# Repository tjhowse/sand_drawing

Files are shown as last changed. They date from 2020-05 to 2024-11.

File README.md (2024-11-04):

# Huh?

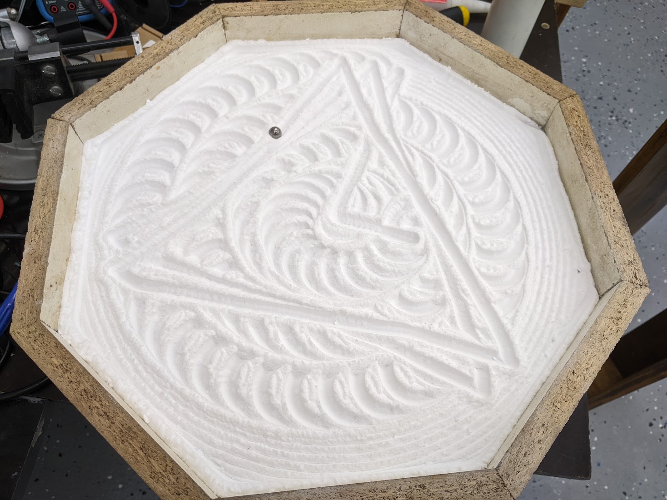
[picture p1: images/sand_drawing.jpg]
a photo of the sand drawing robot


So you've been reading about all the benefits of this "mindfulness" thing and you want to give it a try.
You do some research and learn it requires "meditation", "introspection" and other kinds of tedious woo.
Who has time for that? It's {current_year} for christ's sake! I don't want a tiny tray of rocks and sand
on my desk to rake around. Surely there's some turn-key solution to this problem already.

That's what this project is for. Outsource responsibility for an ordered mind to make more time for the important things, like computer games. And croissants.

# Oh

This project (will contain/contains) all the knowledge you will need to build your own sand drawing robot. Heavily inspired by the likes of [Sandsara](https://www.kickstarter.com/projects/edcano/sandsara) and [Sisyphus](https://sisyphus-industries.com/). It's a robot that moves a ball around in a bed of sand to draw cool patterns. The patterns can be updated via wifi, and it can cycle through them, you can create your own, etc, etc. This project is open source, cheap, and hopefully as easy as possible to build.

# Building it

## Skills required

This isn't a Lego set. You'll need to have access to the following skills:

* Basic woodworking,
* Intermediate soldering,
* Following technical instructions,
* Drilling a hole sideways through steel rod,
* Recovering from setbacks.

I'll do my best to make the instructions as comprehensive and comphrehensible as I can. I appreciate any and all feedback.

## Videos

[Playlist on Youtube.](https://www.youtube.com/playlist?list=PLT7ckgz8vcoY2YFqqQTA0kUofwehtqQul) Maybe worth watching.

## PCB

The PCB is quite simple and cheap. PCBWay generously sponsored a production run of the v1.2 PCBs and they came out perfect. You can order the PCB using [this link](https://www.pcbway.com/project/shareproject/Sand_Drawing_Robot_control_board_344d0ab2.html) and I'll get a small cut. PCBWay asked me to review the board in a youtube video and link it in the readme, but required no further quid pro quo.

## Build logs

For now the build logs are on [my wiki](https://wiki.tjhowse.com/doku.php?id=projects:sand_drawing:overview). Over time they'll morph into actual instructions and end up in this repo.

## Bill of materials

None of these parts are particularly hard to find. Check ebay and whatnot. Try to buy local if you can. It's hard to guess how much it will all cost in total, but I've tried to design everything to be as economical as possible. Excluding the housing I would (very roughly) estimate the BoM to come out to around AUD$200. The housing could be as cheap as AUD$50 (Melamine board, polycarbonate) or as expensive as you want, with lacquered hardwood and tempered glass.

    These bills of material are slightly out of date. Consult the youtube videos.

### Mechanical
| Item | Type | Count | Note |
| ---- | ---- | ----- | ---- |
| Laser cut parts | Various | Many | The current best solution is made from 3mm laser cut plywood. A 3D printed variant is quite possible. |
| Stepper pulley | GT2-20, 12.35mm high | 2 | My steppers had pulleys from the factory. |
| Belt | S2M belt 120mm | 2 | S2M ≈ GT2. |
| Belt | S2M belt 278mm | 1 | |
| Shaft 1 | 8mm x 90mm | 1 | Mild steel is easier to cross-drill than stainless. |
| Shaft 2 | 8mm x 33mm | 1 | |
| Bearing | 608 | 6 | Cheap skate bearings are fine. |
| Washers | 8mm ID, 15.7mm OD | 5 | OD not critical, but it must not rub on outer race of bearings. |
| Washers | 3mm ID, 6.8mm OD | 12 | |
| Bolts | M3x12mm | 8 | I used all 20mm and cut them to length. |
| Bolts | M3x20mm | 2 | |
| Nylock nuts | M3 | 2 | Nylock not critical. |
| Pins | 2mm diameter | 5 | Roll pins would be best, I used nails. +1 extra for pinning shaft 1 into the bearings. |
| Magnets | 12mm diameter, 2mm high neodymium | 2-4 | Situational dimensions. Get a variety of sizes to aid experimentation. |
| Cable ties | 200mm x 4.6mm Nylon | 2 | Dimensions not critical. |

### Electrical
| Item | Type | Count | Note |
| ---- | ---- | ----- | ---- |
| Microcontroller | ESP-WROOM-32D | 1 | Wifi and bluetooth built-in |
| Stepper motor | NEMA-17 | 2 | 200 steps/revolution, around 40mm long, at least 30 N.cm of holding torque. It's not critical, really. |
| Stepper driver | Pololu pinout | 2 | A4988, DRV8825 or TMC2100 in [increasing order of preference](https://github.com/tjhowse/sand_drawing/issues/6) |
| PCB | Custom made | 1 | The design is [here](./pcb/sand_drawing). It's easier and cheaper to have one made than you [might imagine](./pcb/sand_drawing/README_PCB.md).
| Hall effect sensors | SS49E | 2 | Used for detecting arm position. |
| PSU | 12v DC 1A | 1 | A wall wart should be fine. |
| Stepper driver socket | 16x1 2.54mm female | 2 | https://au.rs-online.com/web/p/pcb-sockets/2304893/ |
| Stepper motor socket | 4x1 3.5mm | 2 | https://au.rs-online.com/web/p/pcb-headers/8971039/ |
| Stepper motor plug | 4x1 3.5mm | 2 | https://au.rs-online.com/web/p/pcb-terminal-blocks/8971004/ |
| Optoswitch socket | 3x1 3.5mm | 2 | https://au.rs-online.com/web/p/pcb-headers/8971020/ |
| Optoswitch plug | 3x1 3.5mm | 2 | https://au.rs-online.com/web/p/pcb-terminal-blocks/8971001/ |
| Power socket | 2x1 3.5mm | 1 | https://au.rs-online.com/web/p/pcb-headers/8971026/ |
| Power plug | 2x1 3.5mm | 1 | https://au.rs-online.com/web/p/pcb-terminal-blocks/8970998/ |
| Buttons | 6mm | 2 | https://au.rs-online.com/web/p/tactile-switches/1359534/ |
| UART Header | 3x1 2.54mm male | 1 | https://au.rs-online.com/web/p/pcb-headers/8967364/ |
| 12VDC Barrel socket | 2.1mm pin | 1 | https://au.rs-online.com/web/p/dc-power-sockets/0448370/ |

### Enclosure
| Item | Type | Count | Note |
| ---- | ---- | ----- | ---- |
| Base | Wooood? | 1 | Holds the steppers and circuitry. |
| Top | Wooood? | 1 | Any convex polygon should work. |
| Bed | Glass? | 1 | |
| Lid | Glass | 1 | |
| Sand | Sand | 31378908 | < 100 μm grains, dry.

# Flashing

To flash the software onto the ESP32 you'll need to use the provided scripts `flash32.sh` and `write32.sh`. You'll have to update them with the current version of micropython and the device name of your serial port adapter. When flashing micropython you'll need to hold down the IO0 button while connecting power, then release it five or so seconds after powering on. You can then run `flash32.sh` and it'll write the "OS" onto the chip. Then you can repower again and run `write32.sh` to load the project's scripts onto the board.

# Communication
The ESP-WROOM-32 has wifi and BLE built in. Currently the robot connects to a wifi network, then an MQTT server, to receive commands. Bluetooth should also be possible in the future.

## MQTT Topics
There are a few topics that the robot listens to. Each topic starts with `{secrets.mqtt_root}/sand_drawing/`. I suggest you publish patterns/generators with the retain bit so the robot starts up and then begins that pattern.
| Topic | Example payload | Description |
| ----  | --- | --- |
| `pattern` | `G28 X,G28 Y,G1 X0 Y175,G1 X123 Y123,G1 X175 Y0,J0 2` | Starts drawing the pattern defined by the GCODE in the payload. |
| `generator` | [Here](./pub_gen.py#L82) | Starts drawing the pattern defined by the generator in the payload. See below for details on generators. |
| `save_generator` | `1.pat {generator string}` | Saves the generator to a file in the robot's flash storage. The file extension must be `.pat`. A blank string will erase the generator. |
| `run_generator` | `1.pat` | Starts drawing the previously saved generators. |
| `delete_generator` | `1.pat` | Deletes a generator saved to the robot. |
| `list_generators` | N/A | Publishes a list of filenames to `generator_list` topic. |
| `shuffle_generators` | `3600` | Randomly picks a saved generator and starts drawing it. Optionally provide a number of seconds before choosing another random generator |

# Configuration
There are some files you'll need to edit before your robot will work for you, probably.
[#TODO populate this section.](https://github.com/tjhowse/sand_drawing/issues/13)

# Pattern definition
There are currently two ways to design patterns for the robot.

## GCODEs
This is a sequence of coordinates that define the path of the ball, as well as changing modes and looping. The following GCODES are currently supported. GCODES are separated by a comma.

| Name | GCODE | Example | Description |
| ---- | ----- | --- | --- |
| Home axis| G28 | `G28 X,G28 Y,` | Home either the X or Y axis. Any command that needs an absolute position reference will fail unless both axes have been homed first. |
| Move | G1 | `G1 X10 Y50 S100,` | Go to the X and Y coordinates specified at 100mm/s. Currently the [speed field is ignored](https://github.com/tjhowse/sand_drawing/issues/4). The G1 movement mode carefully tracks every step and should be perfectly accurate if your steppers do not slip. |
| Fast move | G0 |  `G0 X10 Y50 S100,` | Same as G1 however the step signal square wave is generated using PWM so some resolution is lost. At time of writing it is not well-supported. It's really fast though. |
| Coordinate mode | G16 | `G16 0,` | This setting is used to control the interpretation of the `X` and `Y` parameters in the G0 and G1 commands. `0`: Raw speed, `1`: Raw angle, `2`: Cartesian (Default), `3`: Polar (unimplemented) |
| Jump | J0 | `J0 3,` | This jumps to the specified line in the GCODE-defined pattern. Used for creating loops. |
| Absolute coordinate mode | G90 | `G90` | Puts the robot into absolute movement mode. Coordinates in G0/G1 commands are interpreted as absolute position references. (Default) |
| Relative coordinate mode | G91 | `G91` | Puts the robot into relative movement mode. Coordinates in G0/G1 commands are interpreted as movement vectors from the previous position. |

## Generators
You can define a pattern using a python generator function. [Examples here](./pub_gen.py). This is probably the best option for non-trivial patterns.

### Tread lightly
Keep the target hardware in mind when writing generators. It's very resource-constrained. Try to limit RAM usage, and think hard before `import`ing anything. There are some [helper functions](./generator_libs.py) and [constants](./constants.py) in-scope that you can use.

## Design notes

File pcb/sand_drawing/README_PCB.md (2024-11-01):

# PCB Changelog

## v1.2
### Changes
* Fixing footprints for new vreg circuits
* Updated electronics BoM

## v1.1
### Changes
* Connected all stepper driver control pins to ESP
* Changed vreg circuit from an AMS1117-3.3 to an AP63203 with higher current capacity
* Add thermal relief to ESP32 ground pins for easier hand soldering

## v1.0
### Changes
Initial implementation

### Bugs
* Shouldn't use GPIO9 - it is used internally too.
* Pin 7 (IO35) is input-only, can't use that for A2D. - Done.
* Must pull SLP and RST on stepper drivers high. - Done.
* vreg too small, or wired wrong? Only outputs 2.7 Vout at 12 Vin - Done.
* Make sure opto inputs are on ADC-friendly pins. - Done
* Reduce width of ground tie on ESP for easier soldering. - Done.

# ESP-WROOM-32 notes

Minimal implementation on page 15:
https://www.espressif.com/sites/default/files/documentation/esp32-wroom-32d_esp32-wroom-32u_datasheet_en.pdf
A minimal wiring demo:
https://www.youtube.com/watch?v=J10J_7Ap6Oo

# EMC2100 SilentStepStick

These things seem like a bit of a pain in the arse, TBH. I hope they're good.

FAQ:
https://learn.watterott.com/silentstepstick/faq/

# Manufacture

This board is designed for manufacture with PCBWay or JLC. Parts selection, BOM and whatnot are set up for easy manufacture. You should only need to solder on the ESP-WROOM-32D (if using JLC) and headers. All the fiddly little SMD stuff can be done for you, quite cheaply.

## PCBWay-specific notes

You should be able to order a PCB with all the SMD components, including the ESP32) with (this)[https://www.pcbway.com/project/shareproject/Sand_Drawing_Robot_control_board_344d0ab2.html] link. I get a 10% cut.

## JLC-specific notes

If you regenerate the footprint position files you'll need to manually change the header line from:
```
Ref,Val,Package,PosX,PosY,Rot,Side
```
To:
```
Designator,Val,Package,Mid X,Mid Y,Rotation,Layer
```
as per https://support.jlcpcb.com/article/84-how-to-generate-the-bom-and-centroid-file-from-kicad

Odds are you'll need to change the rotation of U2 to 180 degrees, too. Be SUPER CAREFUL at EACH STEP
of the ordering process and you should be OK.

See also https://support.jlcpcb.com/article/84-how-to-generate-the-bom-and-centroid-file-from-kicad for
instructions on how to properly format the BOM spreadsheet for JLC PCB to ingest.

As of 2020-05-30 the price to have five of these boards made, with VREG, resistors, capacitors and diodes
populated was AUD$22.60. This included some discounts and whatnot. Express postage to Australia was AUD$28.03.

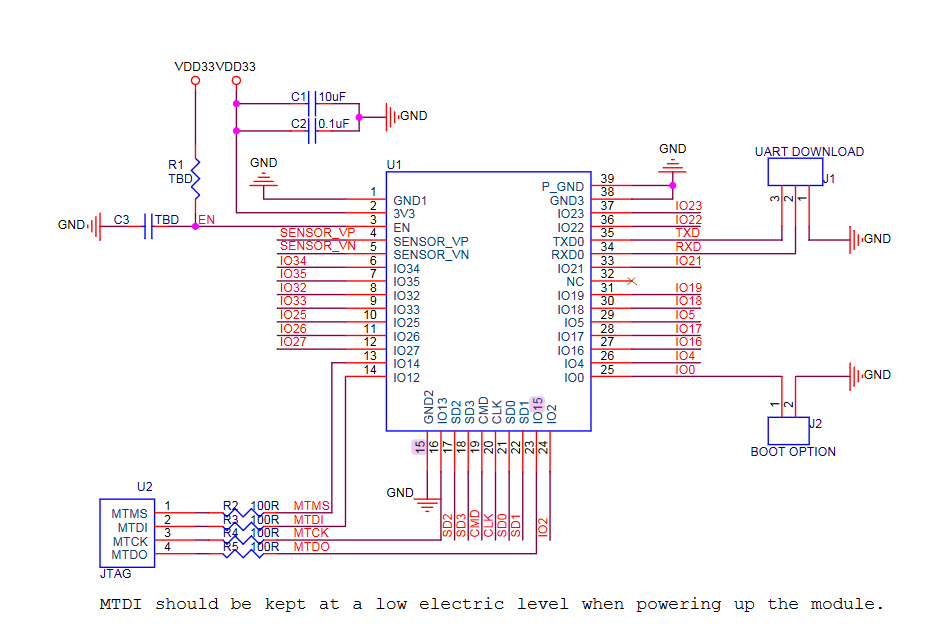
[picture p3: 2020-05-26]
pcb/sand_drawing/modules/minimal_reference.png

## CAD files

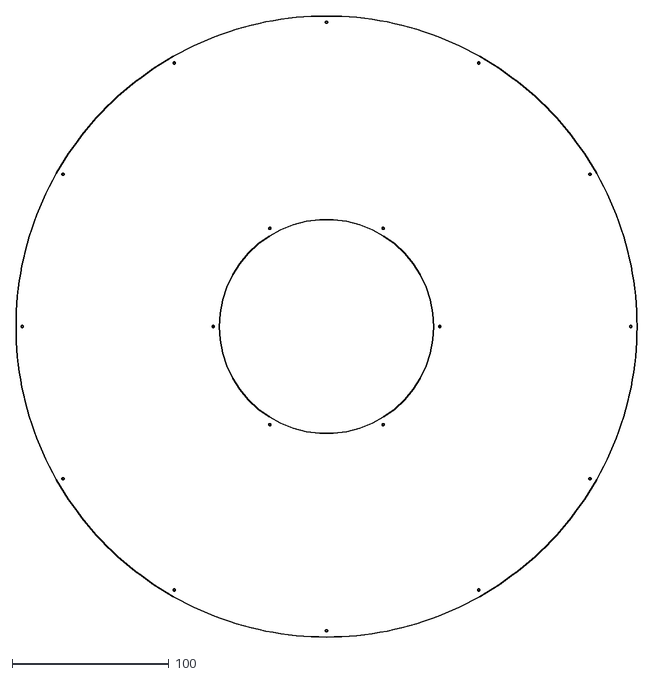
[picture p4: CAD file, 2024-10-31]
scad/lasercut_v2_dxfs/enc_platform_2_x1.dxf
396.0 x 396.0

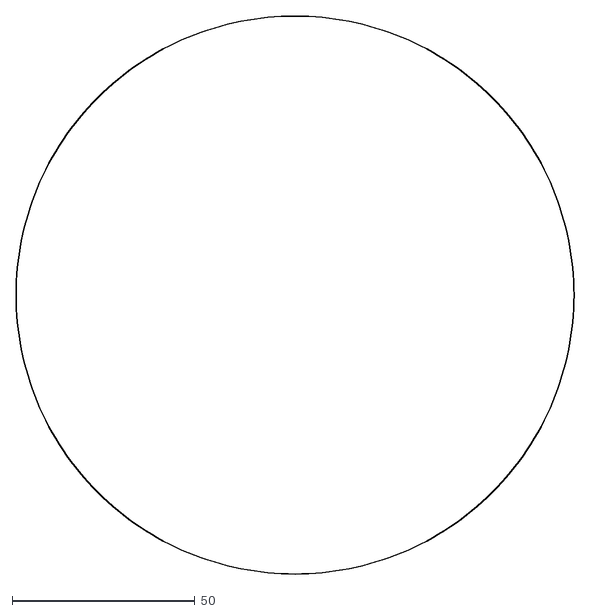
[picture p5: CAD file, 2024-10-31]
scad/lasercut_v2_dxfs/enc_base_1_x1.dxf
152.6 x 152.6

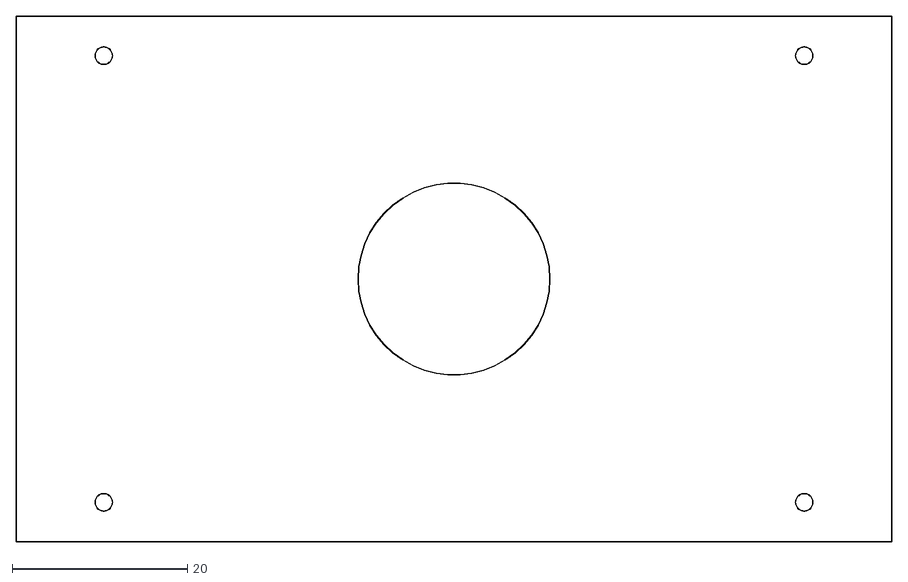
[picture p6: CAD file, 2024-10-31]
scad/lasercut_v2_dxfs/base_lasercut_x2.dxf
100.0 x 60.0

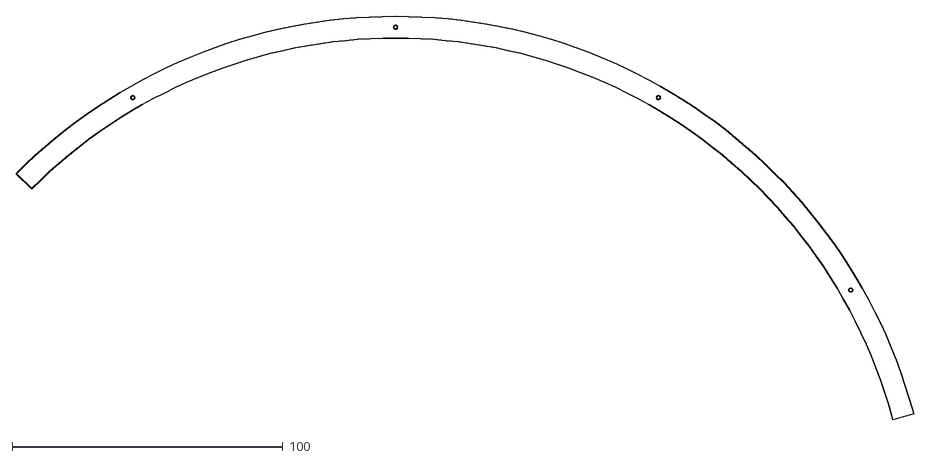
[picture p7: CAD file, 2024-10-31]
scad/lasercut_v2_dxfs/enc_big_ring_third_x30.dxf
331.2 x 148.8

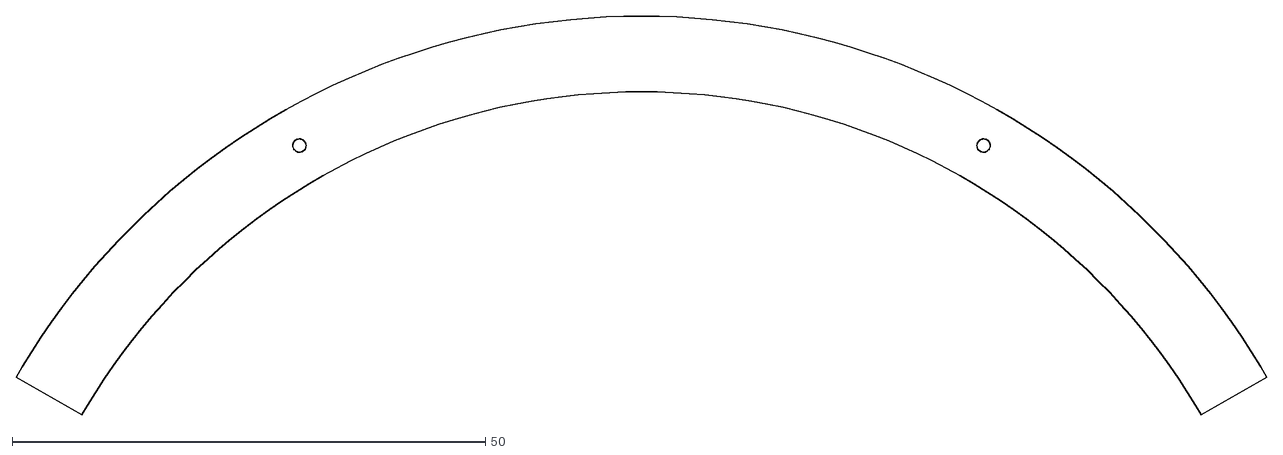
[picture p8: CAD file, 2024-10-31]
scad/lasercut_v2_dxfs/enc_little_ring_third_x60.dxf
132.2 x 42.2

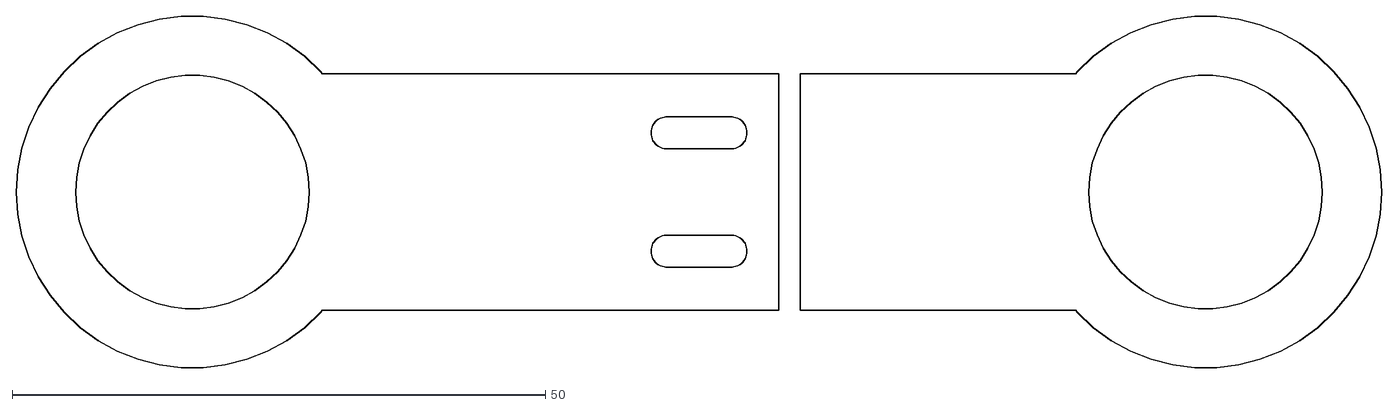
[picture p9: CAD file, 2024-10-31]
scad/lasercut_v2_dxfs/arm_1_lasercut_adjustable.dxf
128.0 x 32.9

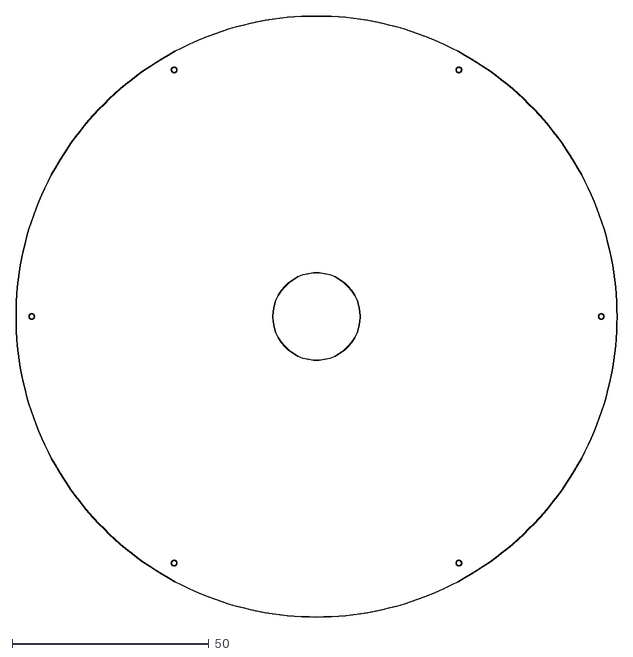
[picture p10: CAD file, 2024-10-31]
scad/lasercut_v2_dxfs/enc_base_2_x1.dxf
152.6 x 152.6

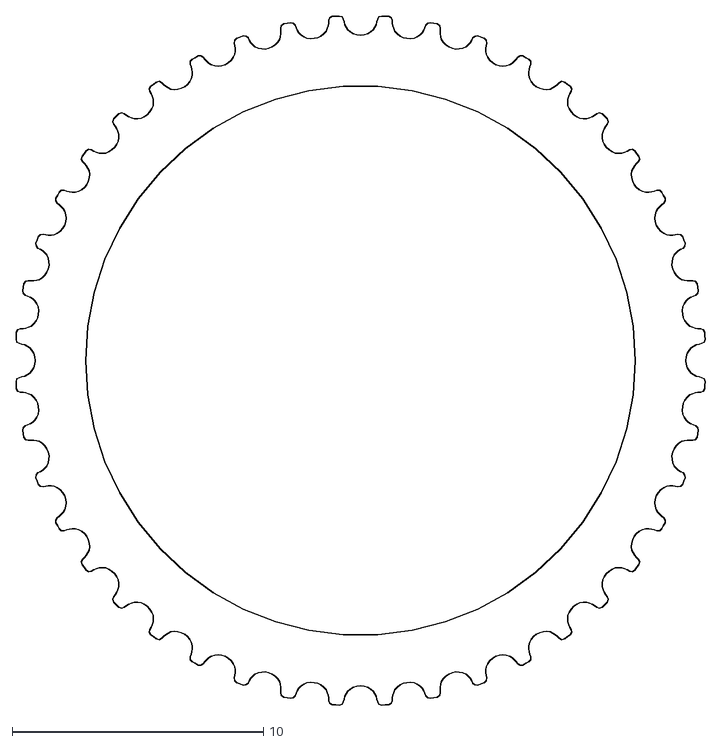
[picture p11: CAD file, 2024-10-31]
scad/lasercut_v2_dxfs/holders.dxf
27.4 x 27.4

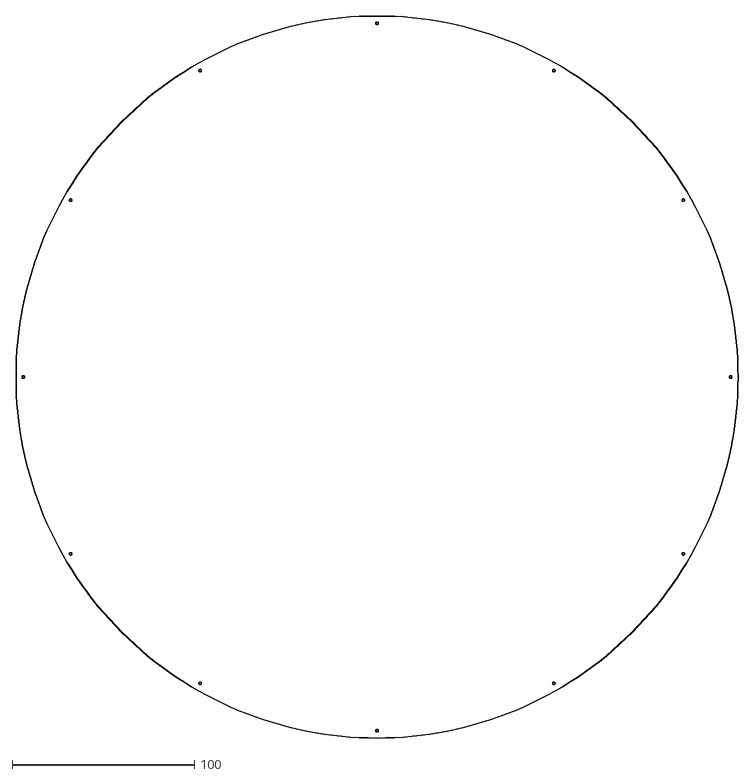
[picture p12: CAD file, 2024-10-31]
scad/lasercut_v2_dxfs/enc_bed_x1.dxf
396.0 x 396.0

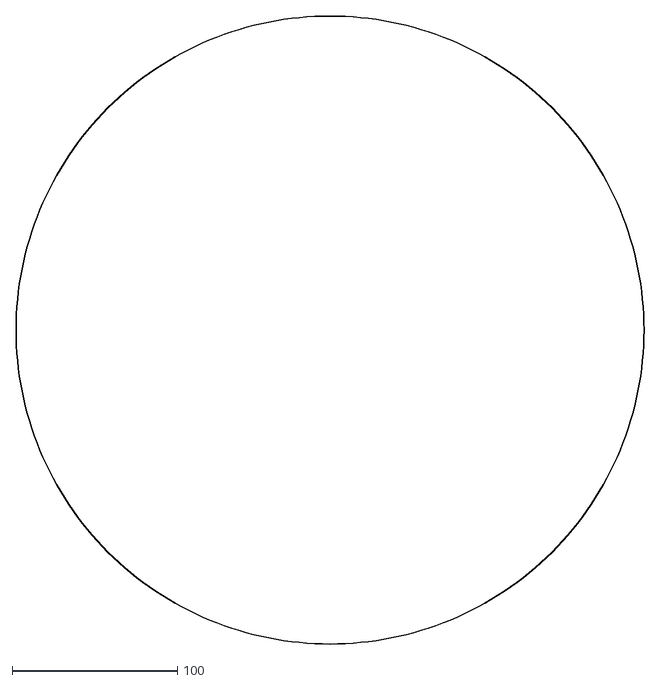
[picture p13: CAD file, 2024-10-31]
scad/lasercut_v2_dxfs/enc_bed_felt_x1.dxf
380.0 x 380.0

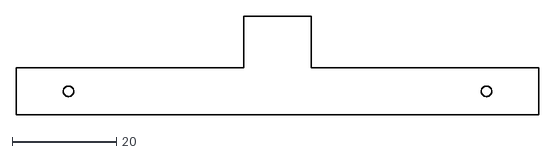
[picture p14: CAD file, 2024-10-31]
scad/lasercut_v2_dxfs/base_guide_lasercut_x4.dxf
100.0 x 18.9

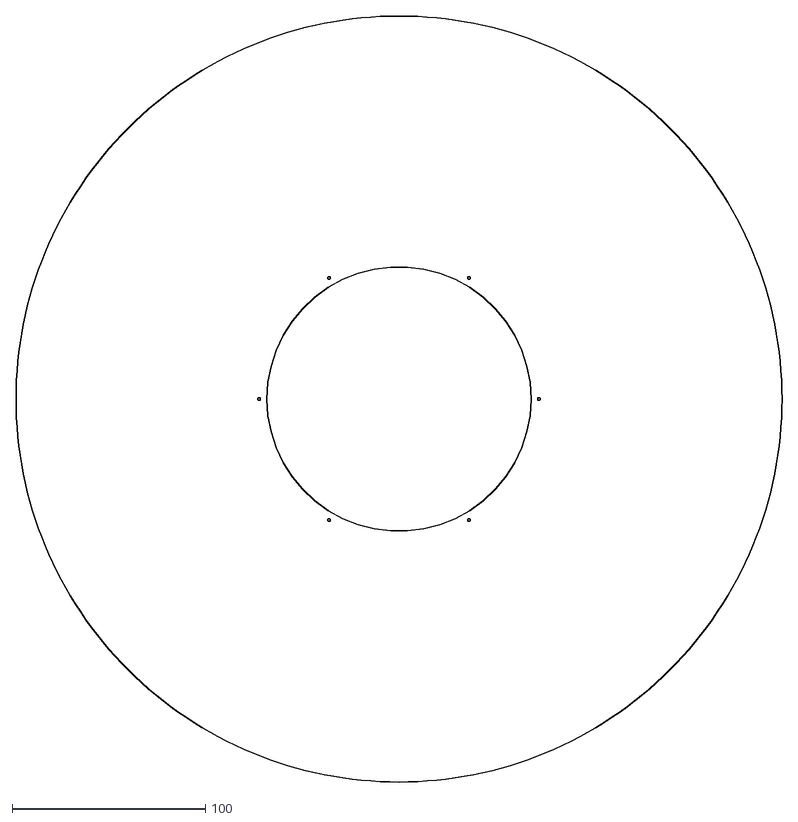
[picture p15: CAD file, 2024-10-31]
scad/lasercut_v2_dxfs/enc_platform_1_x1.dxf
396.0 x 396.0

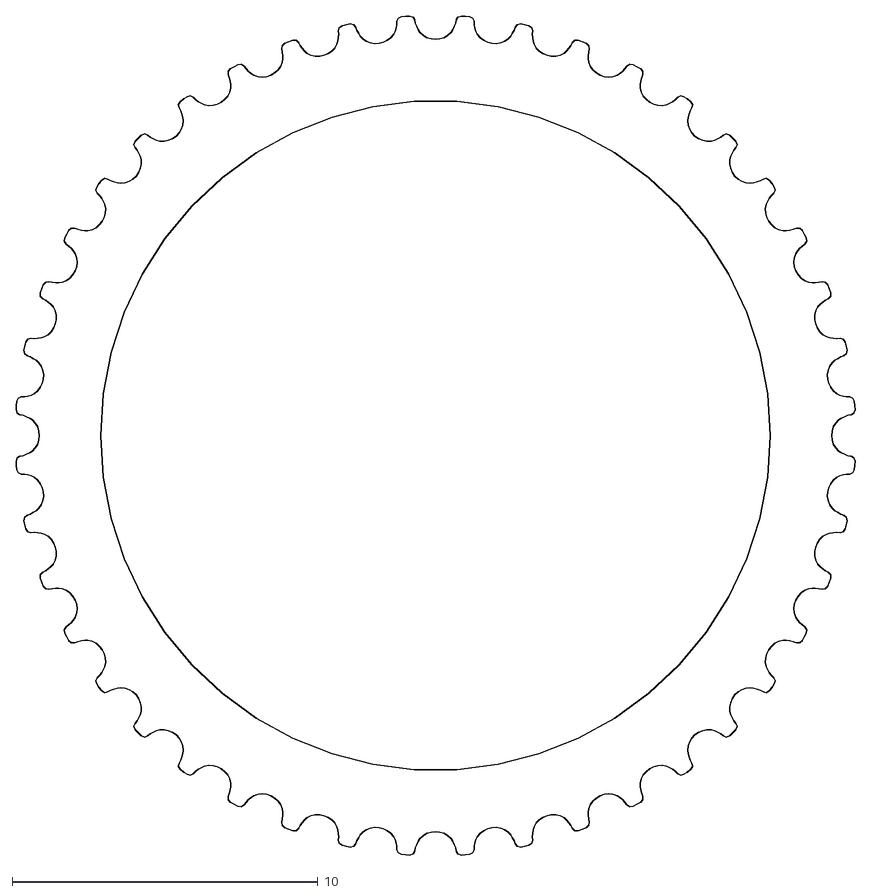
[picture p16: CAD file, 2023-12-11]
scad/lasercut_v2_dxfs/arm_1_pulley_lasercut_x2.dxf
27.4 x 27.4

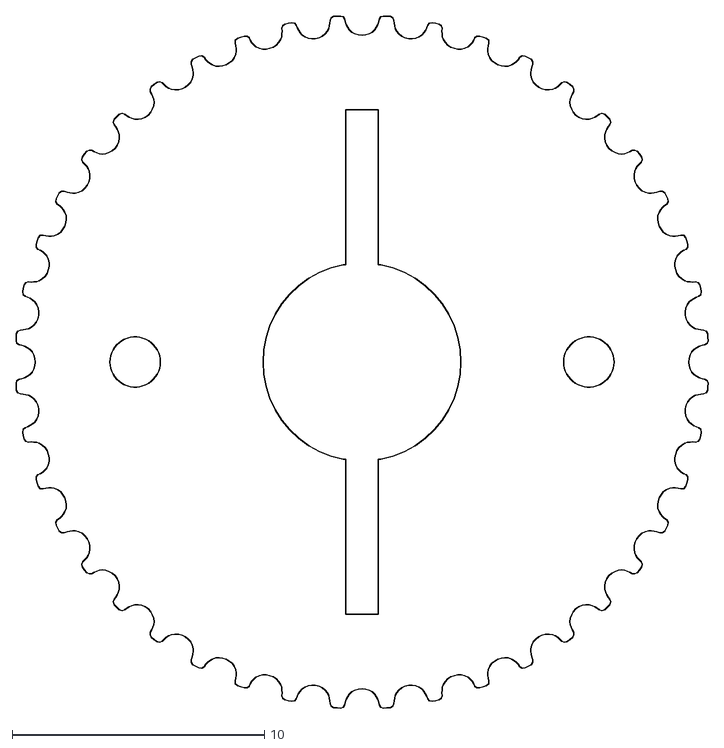
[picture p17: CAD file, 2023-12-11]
scad/lasercut_v2_dxfs/shaft_1_drive_pulley_slot_x3.dxf
27.4 x 27.4

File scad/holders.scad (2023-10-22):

include <Pulley_T-MXL-XL-HTD-GT2_N-tooth.scad>

id_fudge = 0.2;
608_z = 7;
608_id = 8;
608_od = 22+id_fudge;
$fn=50;
stepper_slot = 3;
wt = 3;


n17_hole_spacing = 31;
n17_hole_dia = 3+id_fudge;
n17_center_hole_dia = 22+id_fudge;
n17_xy = 42;
n17_z = 37.5;
n17_pulley_d = 12.25;
n17_pulley_z = 10.7;
n17_pulley_z_offset = 6.8;
n17_belt_guide_z = 1.7;

stepper_1_offset = 608_id/2+n17_xy/2+stepper_slot/2;
stepper_2_offset = stepper_1_offset;

bearing_retain_lip = 0.5;

holder_z = 608_z+bearing_retain_lip;
holder_x = stepper_1_offset + stepper_2_offset + n17_hole_spacing + n17_hole_dia + 2*wt + stepper_slot;
holder_y = n17_hole_spacing + n17_hole_dia + 2*wt;

belt_z = 4.5;
belt2_z = 6.5;

shaft_1_drive_pulley_dia = 27;
shaft_1_drive_pulley_z_top_belt_guide = 0.5;
shaft_1_drive_pulley_z_bottom_belt_guide = 0.5;
shaft_1_drive_pulley_z = belt_z+shaft_1_drive_pulley_z_top_belt_guide + shaft_1_drive_pulley_z_bottom_belt_guide;

shaft_2_drive_pulley_z_top_belt_guide = 0.5;
shaft_2_drive_pulley_z_bottom_belt_guide = 0.5;
// Some extra z height to encapsulate the bearings.
shaft_2_drive_pulley_z_extra_z = 1.3;

shaft_2_driven_pulley_z_top_belt_guide = 1;
shaft_2_driven_pulley_z_bottom_belt_guide = 1;
shaft_2_driven_pulley_z = belt2_z + shaft_2_driven_pulley_z_top_belt_guide + shaft_2_driven_pulley_z_bottom_belt_guide;

shaft_2_drive_pulley_z = belt_z+belt2_z+shaft_2_drive_pulley_z_top_belt_guide+shaft_2_drive_pulley_z_bottom_belt_guide+n17_belt_guide_z+shaft_2_drive_pulley_z_extra_z;
washer_z = 1.3;
washer_d = 18.8;

// Slightly undersized for two 27mm pulleys and a 278mm belt, but the tensioner
// will let us expand it to perfection.
// https://www.omnicalculator.com/physics/belt-length
// Belt length = π/2 × (DL + DS) + 2L + (DL - DS)^2/(4L)

// DL is the diameter of the larger pulley (here 20 inches);
// DS is the diameter of the smaller pulley (here 6 inches); and
// L is the distance between the center of the pulleys.

arm1_axis_offset = 95;
arm1_z = 608_z*2+bearing_retain_lip;
arm1_x = 2*wt+608_od+arm1_axis_offset+608_id;
arm1_y = 2*wt+608_od;

pin_r = 1;
pin_x = 20;


module n17_holes(slot = 0)
{
    translate([-slot/2,0,0])
    {
        hull()
        {
            cylinder(r=n17_center_hole_dia/2,h=100);
            translate([slot,0,0]) cylinder(r=n17_center_hole_dia/2,h=100);
        }
        hull()
        {
            translate([-n17_hole_spacing/2,-n17_hole_spacing/2,0]) cylinder(r=n17_hole_dia/2,h=100);
            translate([-n17_hole_spacing/2+slot,-n17_hole_spacing/2,0]) cylinder(r=n17_hole_dia/2,h=100);
        }
        hull()
        {
            translate([-n17_hole_spacing/2,n17_hole_spacing/2,0]) cylinder(r=n17_hole_dia/2,h=100);
            translate([-n17_hole_spacing/2+slot,n17_hole_spacing/2,0]) cylinder(r=n17_hole_dia/2,h=100);
        }
        hull()
        {
            translate([n17_hole_spacing/2,-n17_hole_spacing/2,0]) cylinder(r=n17_hole_dia/2,h=100);
            translate([n17_hole_spacing/2+slot,-n17_hole_spacing/2,0]) cylinder(r=n17_hole_dia/2,h=100);
        }
        hull()
        {
            translate([n17_hole_spacing/2,n17_hole_spacing/2,0]) cylinder(r=n17_hole_dia/2,h=100);
            translate([n17_hole_spacing/2+slot,n17_hole_spacing/2,0]) cylinder(r=n17_hole_dia/2,h=100);
        }
    }
    translate([0,0,-n17_pulley_z+holder_z-n17_pulley_z_offset]) #cylinder(r=n17_pulley_d/2, h=n17_pulley_z);
    translate([0,0,-n17_pulley_z+holder_z-n17_pulley_z_offset-n17_belt_guide_z]) #cylinder(r=16/2, h=n17_belt_guide_z);
    // translate([-stepper_slot/2,0,0]) %cube([n17_xy, n17_xy,100], center =true);

}


module bearing(fill, cut_kerf=0)
{
    difference()
    {
        cylinder(h = 608_z, r = 608_od/2-cut_kerf);
        if (fill != 0) cylinder(h = 608_z, r = 608_id/2);
    }
}

module bearing_holder()
{
    difference()
    {
        cylinder(r=608_od/2+wt, h=608_z);
        bearing(1);
    }
}

// bearing(0);

module shaft_1_drive_pulley(fast=false)
{
    if (!fast)
    {
        difference()
        {
            translate([0,0,shaft_1_drive_pulley_z_top_belt_guide]) pulley ( "GT2 2mm" , GT2_2mm_pulley_dia , 0.764 , 1.494, belt_z, shaft_1_drive_pulley_z_bottom_belt_guide, shaft_1_drive_pulley_z_top_belt_guide);
            translate([0,0,shaft_1_drive_pulley_z/2])rotate([90,0,0]) translate([0,0,-50]) cylinder(r=pin_r,h=100);
        }
    } else {
        cylinder(r=shaft_1_drive_pulley_dia/2, h = shaft_1_drive_pulley_z);
    }
}

module shaft_2_drive_pulley()
{
    difference()
    {
        translate([0,0,shaft_2_drive_pulley_z_bottom_belt_guide]) pulley ( "GT2 2mm" , GT2_2mm_pulley_dia , 0.764 , 1.494,belt_z+belt2_z+n17_belt_guide_z+shaft_2_drive_pulley_z_extra_z, shaft_2_drive_pulley_z_bottom_belt_guide, shaft_2_drive_pulley_z_top_belt_guide);
        translate([0,0,bearing_retain_lip]) cylinder(r=608_od/2,h=100);
        cylinder(r=(washer_d*1.1)/2,h=100);
    }
    // %cylinder(r=shaft_1_drive_pulley_dia/2, h = shaft_2_drive_pulley_z);
    // translate([0,0,bearing_retain_lip]) #bearing();
    // translate([0,0,bearing_retain_lip+608_z]) #bearing();
}
module shaft_2_driven_pulley()
{
    difference()
    {
        translate([0,0,shaft_1_drive_pulley_z_top_belt_guide]) pulley ( "GT2 2mm" , GT2_2mm_pulley_dia , 0.764 , 1.494, belt2_z, shaft_2_driven_pulley_z_bottom_belt_guide, shaft_2_driven_pulley_z_top_belt_guide);
        translate([0,0,shaft_2_driven_pulley_z/2])rotate([90,0,0]) translate([0,0,-50]) #cylinder(r=pin_r,h=100);
    }
    %cylinder(r=shaft_1_drive_pulley_dia/2, h = shaft_2_driven_pulley_z);
}

module top_holder(bearing_cut_kerf=0)
{
    difference()
    {
        union()
        {
            translate([0,0,holder_z/2]) cube([holder_x, holder_y, holder_z], center = true);
            // cylinder(r=608_od/2+wt, h = 608_z+wt);
        }
        translate([stepper_1_offset,0,0]) n17_holes(stepper_slot);
        translate([-stepper_2_offset,0,0]) n17_holes(stepper_slot);
        translate([0,0,bearing_retain_lip]) bearing(0, bearing_cut_kerf);
        cylinder(r=608_od/2-wt, h = 100);
        #cylinder(r=608_id/2, h = 100);
    }
    // bearing_holder();
    // translate([0,0,-shaft_1_drive_pulley_z-washer_z+bearing_retain_lip]) shaft_1_drive_pulley();
    // translate([0,0,-shaft_1_drive_pulley_z-shaft_2_drive_pulley_z-washer_z]) shaft_2_drive_pulley();
}

module arm1()
{
    // translate([0,0,arm1_z/2]) %cube([arm1_x, arm1_y, arm1_z], center=true);
    difference()
    {
        union()
        {
            translate([arm1_axis_offset/2,0,0]) cylinder(r=608_od/2+wt,h=arm1_z);
            hull()
            {
                translate([arm1_axis_offset/2,0,0]) cylinder(r=608_id/2+wt,h=arm1_z);
                translate([-arm1_axis_offset/2,0,0]) cylinder(r=608_id/2+wt,h=arm1_z);
            }
        }
        translate([arm1_axis_offset/2,0,bearing_retain_lip]) cylinder(r=608_od/2,h=2*608_z);
        translate([arm1_axis_offset/2,0,0]) cylinder(r=608_od/2-wt,h=arm1_z);
        translate([-arm1_axis_offset/2,0,0]) cylinder(r=608_id/2,h=arm1_z);
        translate([-arm1_axis_offset/2,0,arm1_z/2]) rotate([90,0,0]) translate([0,0,-50]) cylinder(r=pin_r,h=100);
    }
    translate([arm1_axis_offset/2+608_od/2+wt,0,0]) optoflag();
}
arm1_split_overlap = 30;
split_point_offset_from_centre = -30;
arm_slot_r = 1.5;
arm_slot_width = 3;
arm_slot_width_total = arm_slot_width + 2*arm_slot_r;

module slot(slot_r = arm_slot_r, slot_h = arm_slot_width)
{
    rotate([90,0,0]) translate([-slot_h/2,0,-50]) hull()
    {
        cylinder(r=slot_r, h=100);
        translate([slot_h,0,0]) cylinder(r=slot_r, h=100);
    }
}

module arm1_split_base()
{
    // This is arm1, but split into two parts for belt tensioning purposes.
    // Base
    translate([arm1_split_overlap,0,0]) difference()
    {
        translate([-arm1_split_overlap,0,0]) arm1();
        translate([0,-50,0]) cube([100,100,100]);
        translate([-arm1_split_overlap,-50,arm1_z/2]) cube([100,100,100]);
        rotate([90,0,0]) {
            translate([-arm_slot_width_total/2-wt, 0, 0]) slot();
            translate([split_point_offset_from_centre+arm_slot_width_total/2+wt+arm_slot_width_total/2, 0, 0]) slot();
        }
    }
}

module arm1_split_end()
{
    // This is arm1, but split into two parts for belt tensioning purposes.
    difference()
    {
        rotate([0,0,180]) arm1();
        translate([0,-50,0]) cube([100,100,100]);
        translate([-arm1_split_overlap,-50,arm1_z/2]) cube([100,100,100]);
        rotate([90,0,0]) {
            translate([-arm_slot_width_total/2-wt, 0, 0]) slot();
            translate([split_point_offset_from_centre+arm_slot_width_total/2+wt+arm_slot_width_total/2, 0, 0]) slot();
        }
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

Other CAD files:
scad/lasercut_v2_dxfs/top_holder_lasercut_x2.dxf
scad/lasercut_v2_dxfs/arm_1_lasercut_adjustable_x4.dxf
scad/lasercut_v2_dxfs/belt_splitter_inner_x1.dxf
scad/lasercut_v2_dxfs/shaft_1_drive_pulley_noslot_x3.dxf
scad/Pulley_T-MXL-XL-HTD-GT2_N-tooth.scad
scad/lasercut_v2_dxfs/arm_2_lasercut_x1.dxf
scad/lasercut_v2_dxfs/belt_splitter_outer_x2.dxf

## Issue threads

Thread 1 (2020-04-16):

Arm1/shaft1 pin cannot be driven out

tjhowse, 2020-04-16:
Fix that by rotating the pin hole 90 degrees about Z. This will make it possible to punch the pin all the way through for disassembly.

tjhowse, 2020-04-19:
Fixed.

Closed 2020-04-19.

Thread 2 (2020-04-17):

Arm1 can flex due to belt tension

tjhowse, 2020-04-17:
The arm1 length adjustment should have a horizontally split overlap, not vertical, such that the bolts holding it together are put under tension by belt tension, not shear. It is easy for the two parts of arm1 to rotate WRT eachother if the bolts aren't done up extremely tight. This droops the arm down and could misalign the end of the arm with the optoswitches.

tjhowse, 2020-04-19:
Fixed!

Closed 2020-04-19.

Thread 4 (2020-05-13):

G1 gcode speed field is ignored

tjhowse, 2020-05-13:
At the moment if you issue a G1 gcode, E.G. "G1 X100 Y100 S1000", the speed parameter (S) is ignored. The steppers only move at DEFAULT_MOVE_SPEED. It should be possible to specify a speed value in a G1 gcode, and for that to control the speed of the endpoint.

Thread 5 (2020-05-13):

Arm 2 enclosure collision possible when homing

tjhowse, 2020-05-13:
In certain initial conditions it is possible for arm2 to strike the edge of an octagonal enclosure during homing. This shouldn't happen or, if it must happen, it should have at least one stepper disabled so the system does not jam.

Consider other optoswitch placements, or other sensors.

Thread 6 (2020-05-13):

Steppers make an audible noise when moving

tjhowse, 2020-05-13:
I would like the system to be as quiet as possible when moving. Evaluate different microstepping, current limit and speed settings to get the system as quiet as possible.

From this point, investigate sound damping and vibration isolation options.

tjhowse, 2020-05-13:
Look at https://www.trinamic.com/support/eval-kits/details/silentstepstick/

tjhowse, 2020-05-19:
https://learn.watterott.com/silentstepstick/faq/ Wow these things are fiddly.

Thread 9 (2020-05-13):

Need an ESP32 circuit and PCB

tjhowse, 2020-05-13:
Now that I'm using an ESP32 I need a circuit and PCB to suit. Consider directly implementing an ESP-WROOM-32D on the PCB rather than using a carrier board. Interface via  usb-to-TTL adaptor (FTDI).

All control I/O on the DRV8825 boards should be connected to GPIO on the ESP32, not just step and direction, we have lots of extra pins available and it would be nice to be able to support changing microstepping in software.

Closed 2020-05-30.

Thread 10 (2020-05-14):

Ball makes a crunching sound as it moves through the sand

tjhowse, 2020-05-14:
When the ball is moving through the sand it makes a quite loud crunching noise. Somehow the Sandsara project are running almost silently, so there's gotta be a trick here.

This is the first test arrangement:
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

The sand (brown) can get trapped between the ball and the bed.

Perhaps something like this might work:
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

This would plough the sand out of the way so it doesn't get trapped.

Another option would be to use a sand with a large, consistent grain size, so the grains are more likely to be shunted aside than trapped.

tjhowse, 2020-05-17:
I've had good success using a finer material - flour. I'll try out some more inert alternatives. Titanium dioxide or a fine sand would be worth a try.

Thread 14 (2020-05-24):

Pattern shuffling can interrupt patterns

tjhowse, 2020-05-24:
The pattern shuffling timer kicks in regardless of whether a pattern has finished drawing or not, and this is bad because the pattern doesn't finish drawing. Consider only shuffling if the pattern finishes. Patterns will have to emit an END gcode at a point at which it could cede control to another pattern.

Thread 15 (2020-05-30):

No drawings for shaft cross-drill dimensions.

tjhowse, 2020-05-30:
There needs to be a drawing showing where the shafts need to be cross-drilled to pin the arms and pulleys in place.

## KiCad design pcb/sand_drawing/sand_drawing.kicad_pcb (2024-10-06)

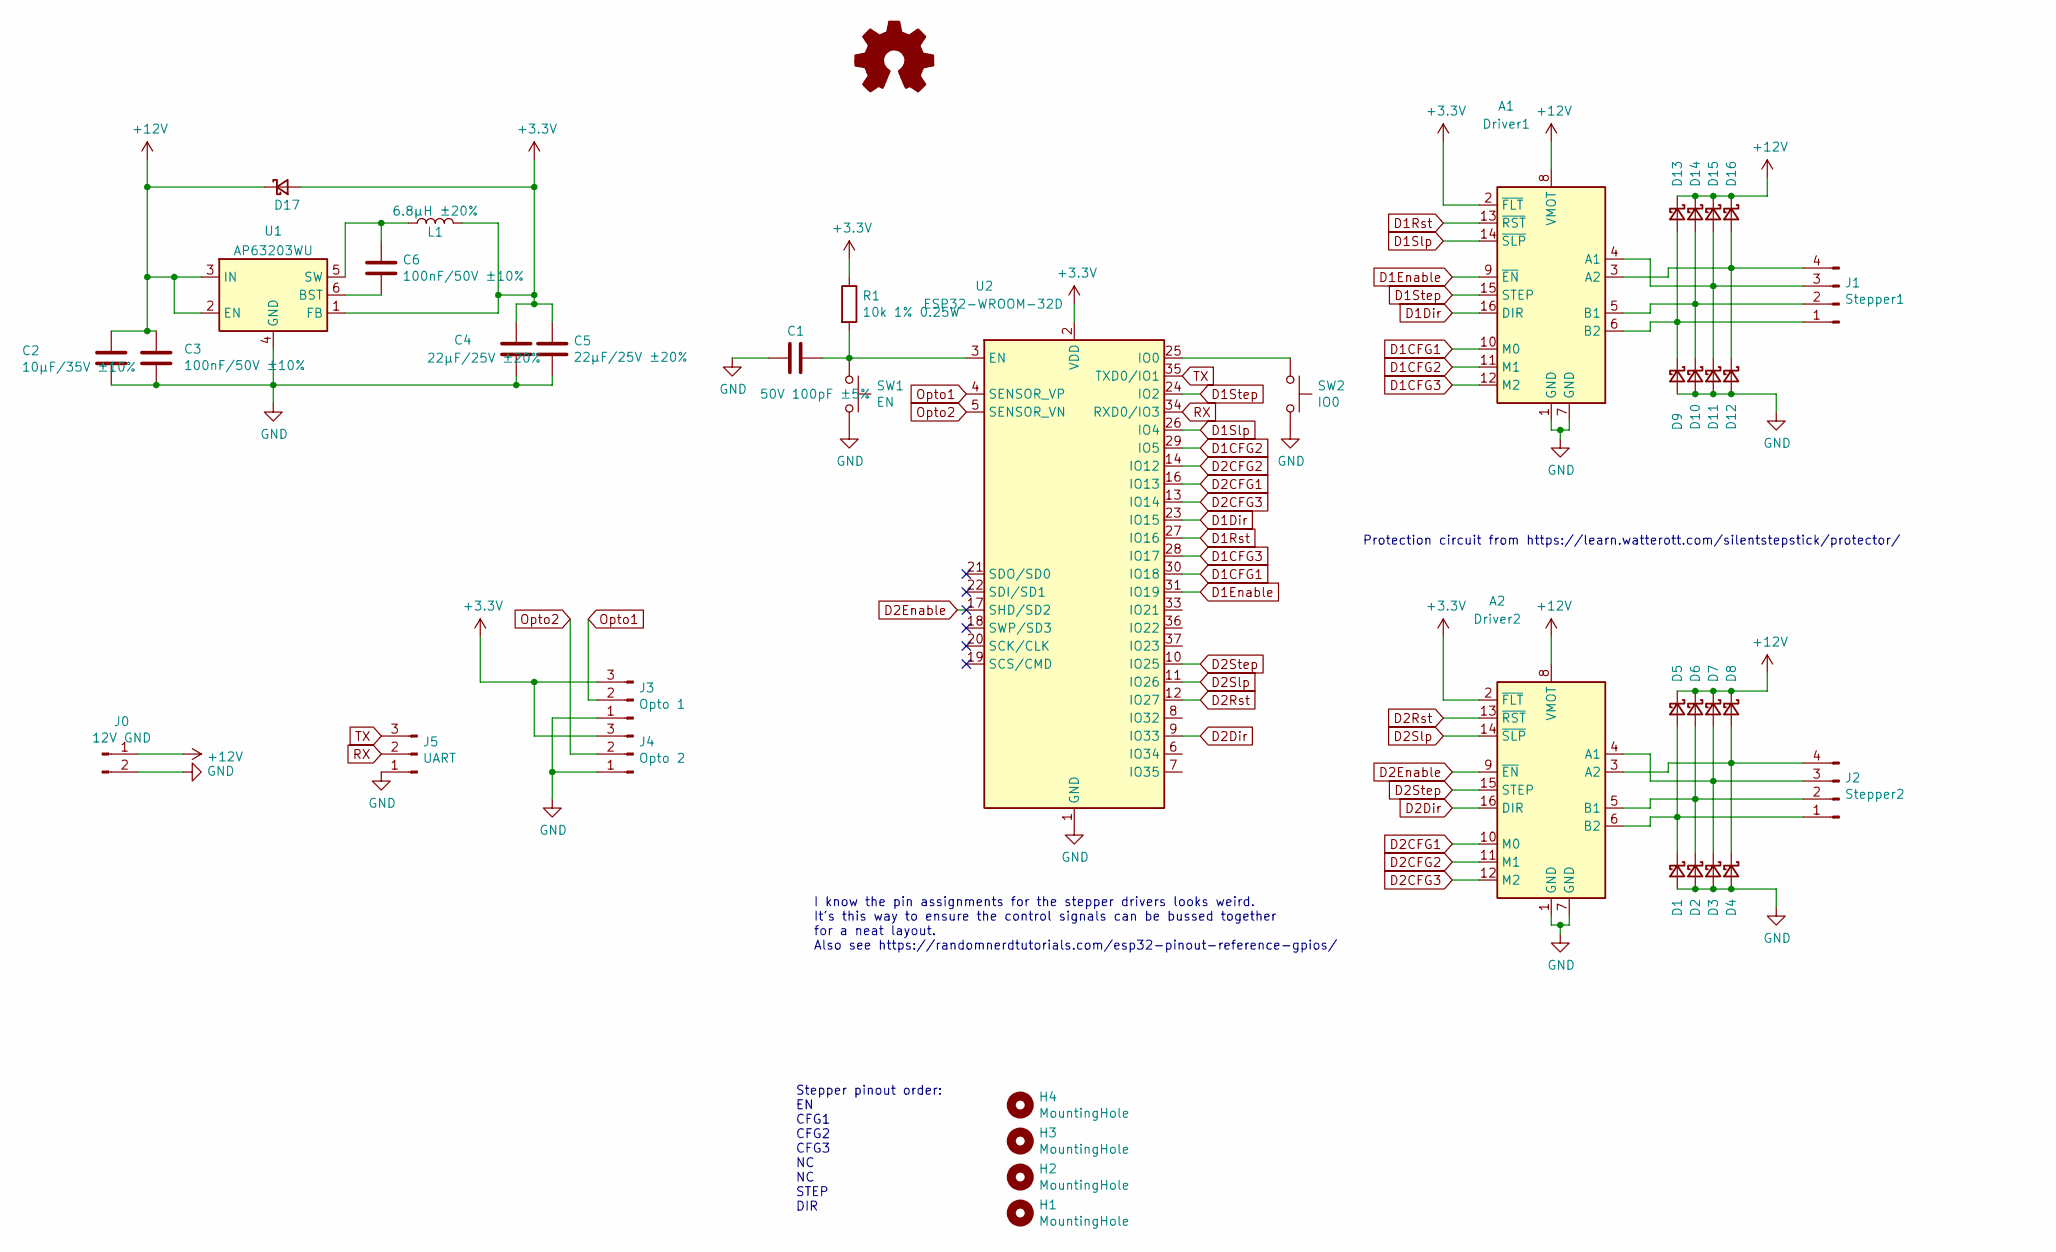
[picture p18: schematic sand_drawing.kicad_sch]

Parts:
A1: Driver1; Pololu_Breakout-16_15.2x20.3mm
A2: Driver2; Pololu_Breakout-16_15.2x20.3mm
C1: 50V 100pF ±5%; C_0805_2012Metric; MPN CL21C101JBANNNC; LCSC C1790
C2: 10µF/35V ±10%; C_1206_3216Metric; MPN CGA5L1X7R1V106K160AE; LCSC C15850
C3, C6: 100nF/50V ±10%; C_0603_1608Metric; MPN CGA3E2X7R1H104K080AA; LCSC C15850
C4, C5: 22µF/25V ±20%; C_1206_3216Metric; MPN C3216X5R1E226M160AB; LCSC C15850
D1, D2, D3, D4, D5, D6, D7, D8, D9, D10, D11, D12, D13, D14, D15, D16, D17: 100V 850mV@2A Schottky Diode; D_SMB; MPN Taiwan Semiconductor SS210; LCSC C14996
H1, H2, H3, H4: MountingHole; MountingHole_3.2mm_M3
J0: 12V GND; PhoenixContact_MCV_1,5_2-G-3.5_1x02_P3.50mm_Vertical
J1: Stepper1; PhoenixContact_MCV_1,5_4-G-3.5_1x04_P3.50mm_Vertical
J2: Stepper2; PhoenixContact_MCV_1,5_4-G-3.5_1x04_P3.50mm_Vertical
J3: Opto 1; PhoenixContact_MCV_1,5_3-G-3.5_1x03_P3.50mm_Vertical
J4: Opto 2; PhoenixContact_MCV_1,5_3-G-3.5_1x03_P3.50mm_Vertical
J5: UART; PinSocket_1x03_P2.54mm_Vertical
L1: 6.8µH ±20%; WURTH_6060; MPN Wurth 74439346068
LOGO1: Logo_Open_Hardware_Small; OSHW-Logo2_14.6x12mm_SilkScreen
R1: 10k 1% 0.25W; R_0603_1608Metric; MPN CRGP0603F10K; LCSC C25804
SW1: EN; SW_PUSH_6mm
SW2: IO0; SW_PUSH_6mm
U1: AP63203WU; TSOT-26-6; MPN AP63203WU-7
U2: ESP32-WROOM-32D; ESP32-WROOM-32; MPN ESP32-WROOM-32D

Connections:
+3V3: A1.2 (~FLT), A2.2 (~FLT), C4.1, C5.1, D17.2 (A), J3.3, J4.3, L1.2, R1.1, U1.1 (FB), U2.2 (VDD)
+12V: A1.8 (VMOT), A2.8 (VMOT), C2.1, C3.1, D5.1 (K), D6.1 (K), D7.1 (K), D8.1 (K), D13.1 (K), D14.1 (K), D15.1 (K), D16.1 (K), D17.1 (K), J0.1, U1.2 (EN), U1.3 (IN)
D1CFG1: A1.10 (M0), U2.30 (IO18)
D1CFG2: A1.11 (M1), U2.29 (IO5)
D1CFG3: A1.12 (M2), U2.28 (IO17)
D1Dir: A1.16 (DIR), U2.23 (IO15)
D1Enable: A1.9 (~EN), U2.31 (IO19)
D1Rst: A1.13 (~RST), U2.27 (IO16)
D1Slp: A1.14 (~SLP), U2.26 (IO4)
D1Step: A1.15 (STEP), U2.24 (IO2)
D2CFG1: A2.10 (M0), U2.16 (IO13)
D2CFG2: A2.11 (M1), U2.14 (IO12)
D2CFG3: A2.12 (M2), U2.13 (IO14)
D2Dir: A2.16 (DIR), U2.9 (IO33)
D2Enable: A2.9 (~EN), U2.17 (SHD/SD2)
D2Rst: A2.13 (~RST), U2.12 (IO27)
D2Slp: A2.14 (~SLP), U2.11 (IO26)
D2Step: A2.15 (STEP), U2.10 (IO25)
GND: A1.1 (GND), A1.7 (GND), A2.1 (GND), A2.7 (GND), C1.2, C2.2, C3.2, C4.2, C5.2, D1.2 (A), D2.2 (A), D3.2 (A), D4.2 (A), D9.2 (A), D10.2 (A), D11.2 (A), D12.2 (A), J0.2, J3.1, J4.1, J5.1, SW1.2, SW2.2, U1.4 (GND), U2.1 (GND), U2.15 (GND), U2.38 (GND), U2.39 (GND)
unnamed: A1.4 (A1), D11.1 (K), D15.2 (A), J1.3
unnamed: A1.3 (A2), D12.1 (K), D16.2 (A), J1.4
unnamed: A1.5 (B1), D10.1 (K), D14.2 (A), J1.2
unnamed: A1.6 (B2), D9.1 (K), D13.2 (A), J1.1
unnamed: A2.4 (A1), D3.1 (K), D7.2 (A), J2.3
unnamed: A2.3 (A2), D4.1 (K), D8.2 (A), J2.4
unnamed: A2.5 (B1), D2.1 (K), D6.2 (A), J2.2
unnamed: A2.6 (B2), D1.1 (K), D5.2 (A), J2.1
unnamed: C6.2, U1.6 (BST)
unnamed: C6.1, L1.1, U1.5 (SW)
unnamed: C1.1, R1.2, SW1.1, U2.3 (EN)
unnamed: SW2.1, U2.25 (IO0)
Opto1: J3.2, U2.4 (SENSOR_VP)
Opto2: J4.2, U2.5 (SENSOR_VN)
RX: J5.2, U2.34 (RXD0/IO3)
TX: J5.3, U2.35 (TXD0/IO1)

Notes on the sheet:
Protection circuit from https://learn.watterott.com/silentstepstick/protector/
I know the pin assignments for the stepper drivers looks weird. It's this way to ensure the control signals can be bussed together for a neat layout. Also see https://randomnerdtutorials.com/esp32-pinout-reference-gpios/
Stepper pinout order: EN CFG1 CFG2 CFG3 NC NC STEP DIR

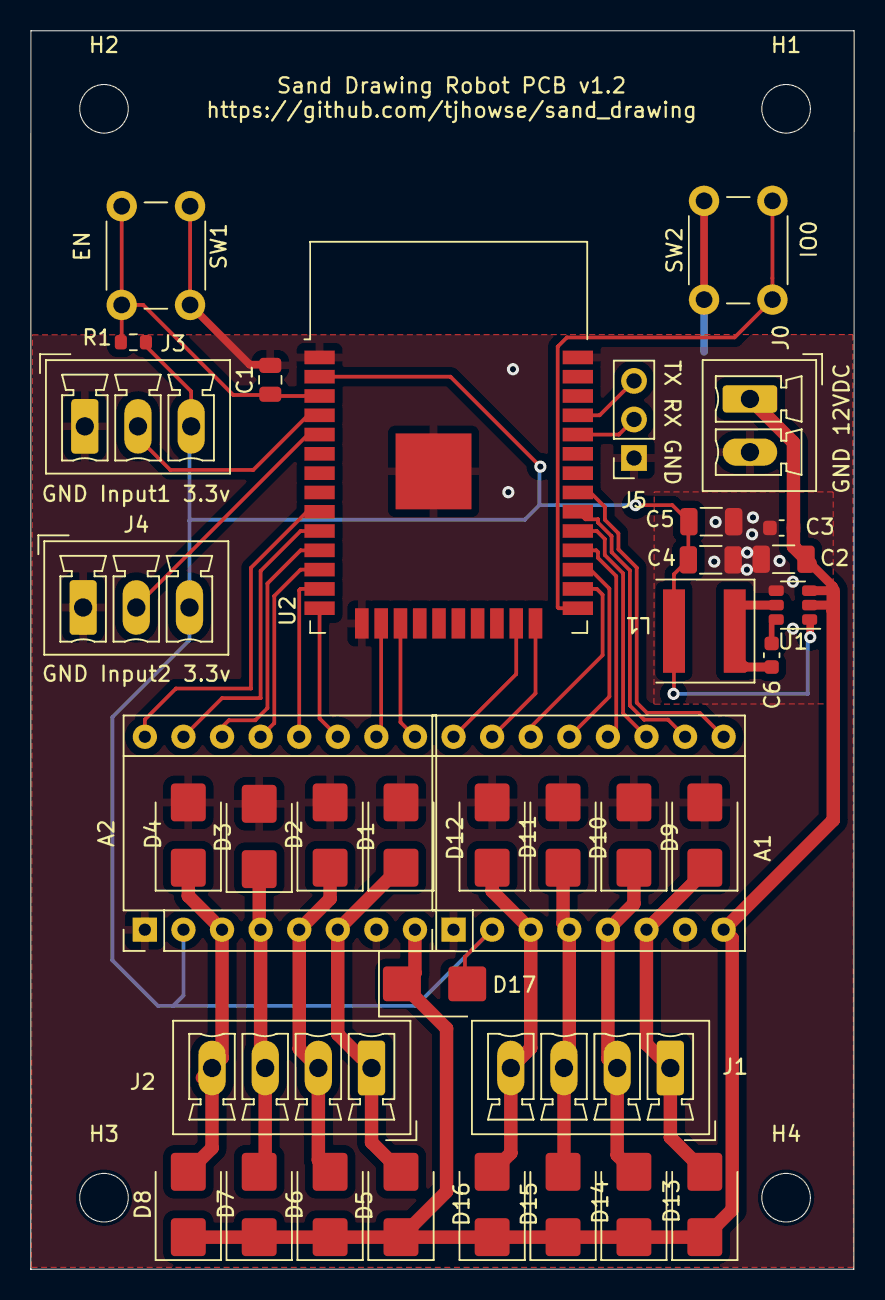
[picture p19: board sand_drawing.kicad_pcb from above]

Board: 2 copper layers, 54.2 x 81.5 mm, 41 parts (0 on the bottom side), 35 nets.

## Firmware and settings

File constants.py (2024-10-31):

import math
MICROCONTROLLER = "board_v1_2"
PWM_STEPPING = False

class StepperPins:
    step = 0
    dir = 0
    enable = 0
    cfg1 = 0
    cfg2 = 0
    cfg3 = 0
    opto = 0
    rst = 0 # Reset
    slp = 0 # Sleep
    hall_effect = False


if MICROCONTROLLER == "d1mini":
    A1S_PIN = 16
    A1D_PIN = 5
    A2S_PIN = 4
    A2D_PIN = 0
    A1O_PIN = 12
    A2O_PIN = 14
elif MICROCONTROLLER == "atom":
    A1S_PIN = 33
    A1D_PIN = 23
    A2S_PIN = 19
    A2D_PIN = 22
    A1O_PIN = 21
    A2O_PIN = 25
elif MICROCONTROLLER == "board_v1":
    A1PINS = StepperPins()
    A1PINS.step = 16
    A1PINS.dir = 4
    A1PINS.enable = 19
    A1PINS.cfg1 = 18
    A1PINS.cfg2 = 5
    A1PINS.cfg3 = 17
    A1PINS.opto = 36
    A1PINS.hall_effect = True

    A2PINS = StepperPins()
    A2PINS.step = 32
    A2PINS.dir = 12
    A2PINS.enable = 27
    A2PINS.cfg1 = 26
    A2PINS.cfg2 = 25
    A2PINS.cfg3 = 33
    A2PINS.opto = 39
    A2PINS.hall_effect = True

elif MICROCONTROLLER == "board_v1_2":
    # Note these pin numbers are the "IOXX" numbers, not the pin numbers
    # on the package.
    A1PINS = StepperPins()
    A1PINS.step = 2
    A1PINS.dir = 15
    A1PINS.enable = 19
    A1PINS.cfg1 = 18
    A1PINS.cfg2 = 5
    A1PINS.cfg3 = 17
    A1PINS.rst = 16
    A1PINS.slp = 4

    A1PINS.opto = 36
    A1PINS.hall_effect = True

    A2PINS = StepperPins()
    A2PINS.step = 25
    A2PINS.dir = 33
    # Pins SCK/CLK, SDO/SD0, SDI/SD1, SHD/SD2, SWP/SD3 and SCS/CMD, namely, GPIO6 to GPIO11 are connected
    # to the integrated SPI flash integrated on the module and are not recommended for other uses
    A2PINS.enable = 9 # SD2, not recommended for use. Might be a mistake.
    A2PINS.cfg1 = 13
    A2PINS.cfg2 = 12
    A2PINS.cfg3 = 14
    A2PINS.rst = 27
    A2PINS.slp = 26

    A2PINS.opto = 39
    A2PINS.hall_effect = True


STEPS_PER_REV = 200
WILD_MODE = False
if WILD_MODE:
    MICROSTEPPING = 1
    DEFAULT_MOVE_SPEED = 180
else:
    MICROSTEPPING = 32
    DEFAULT_MOVE_SPEED = 30

GEAR_RATIO = 44/20
REAL_STEPS_PER_REV = int(STEPS_PER_REV*MICROSTEPPING*GEAR_RATIO)
REAL_STEPS_PER_DEGREE = REAL_STEPS_PER_REV/360
HALF_REAL_STEPS_PER_REV = REAL_STEPS_PER_REV/2

INDEX_CLOSE_ENOUGH = 3
HOME_SPEED = 180

# You'll have to tweak these to suit the exact placement of your optoswitches.
ARM1_HOME_INDEX = 0
ARM1_HOME_ANGLE = 0
# ARM2_HOME_INDEX = REAL_STEPS_PER_REV/2+500 # Too far clockwise
ARM2_HOME_INDEX = REAL_STEPS_PER_REV/2 # this one might be good?
# ARM2_HOME_INDEX = REAL_STEPS_PER_REV/2+500 # Too far counter-clockwise
# ARM2_HOME_INDEX = REAL_STEPS_PER_REV/2-250
ARM2_HOME_ANGLE = 180

# This may need adjustment for your enclosure. Mine's a regular octagon.
# If your enclosure is circular (how fancy) you can simplify the bounds-checking
# in the cnc class.
# ENCLOSURE_VERTEX_COUNT = 8 # Octagon
ENCLOSURE_VERTEX_COUNT = 64 # Circle (ish)
# This is the distance of the verticies from the centre.
ENCLOSURE_RADIUS = 188
ENCLOSURE_VERTICES = []
for i in range(ENCLOSURE_VERTEX_COUNT):
    angle = math.radians(i*(360/ENCLOSURE_VERTEX_COUNT))
    x = math.trunc(ENCLOSURE_RADIUS*math.sin(angle))
    y = math.trunc(ENCLOSURE_RADIUS*math.cos(angle))
    ENCLOSURE_VERTICES += [(x,y)]

# Movements will be split into smaller stepwise movements of this length at most
# Lower numbers mean straighter movements but more processing time.
PATH_SPLIT_SIZE = 0.5

ARM_1_LENGTH = 94
ARM_2_LENGTH = 94

MOVE_MODE_RAW_SPEED = 0
MOVE_MODE_RAW_ANGLE = 1
MOVE_MODE_CARTESIAN = 2
MOVE_MODE_POLAR = 3

COORD_MODE_ABSOLUTE = 0
COORD_MODE_RELATIVE = 1

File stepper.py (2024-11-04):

# pylint: disable=E0401
from constants import *
from utime import ticks_us, ticks_diff
import machine

class stepper():
    # This manages the interface to a stepper
    s = None # The step output Pin object
    d = None # The direction output Pin object
    o = None # The optoswitch input Pin object
    dir = 0 # 0: Clockwise, 1: Counterclockwise
    step_interval = 0 # The number of ticks_us between rising or falling edges of the step pin
    last_step = 0 # The last ticks_us of a rising or falling edge
    index = -1 # 0-x the number of steps
    last_o = 1 # Used for detecting the rising edge of the opto pin
    high_low = 0 # The state of the step pin. 0: low, 1: high
    homing = False
    indexed = False # Do we know the index of our stepper position?
    stepping = False
    debug = True
    target_index = -1
    pwm = None
    prev_err = 0

    def __init__(self, pinconfig, debug=False, name='', home_index=0, home_angle=0):
        self.hall_effect = pinconfig.hall_effect
        self.s = machine.Pin(pinconfig.step, machine.Pin.OUT)
        self.d = machine.Pin(pinconfig.dir, machine.Pin.OUT)
        if self.hall_effect:
            self.o = machine.ADC(machine.Pin(pinconfig.opto))
            self.o.atten(machine.ADC.ATTN_11DB)
            # This stores the peak magnetic flux read by the hall effect sensor.
            self.max_flux = 0
            self.max_flux_index = 0
        else:
            self.o = machine.Pin(pinconfig.opto, machine.Pin.IN)
        self.cfg1 = machine.Pin(pinconfig.cfg1, machine.Pin.OUT)
        self.cfg2 = machine.Pin(pinconfig.cfg2, machine.Pin.OUT)
        self.cfg3 = machine.Pin(pinconfig.cfg3, machine.Pin.OUT)
        self.cfg1.value(1) # 101 - 32x microstepping
        self.cfg2.value(0)
        self.cfg3.value(1)
        self.enabled = machine.Pin(pinconfig.enable, machine.Pin.OUT)
        self.sleep = machine.Pin(pinconfig.slp, machine.Pin.OUT)
        self.sleep.value(1)
        self.reset = machine.Pin(pinconfig.rst, machine.Pin.OUT)
        self.reset.value(1)
        self.set_dir(0)
        self.debug = debug
        self.name = name
        self.home_index = home_index
        self.home_angle = home_angle

    def config(self, new_config):
        # This is used to change the pin configuration of a stepper.
        print("Setting stepper config to: {}".format(new_config))
        print("1")
        self._pin_config(self.cfg1, int(new_config[0]))
        print("2")
        self._pin_config(self.cfg2, int(new_config[1]))
        print("3")
        self._pin_config(self.cfg3, int(new_config[2]))

    def _pin_config(self, pin, value):
        if not value in [0,1]:
            return
        print("to {}".format(value))
        pin.value(value)

    def set_speed(self, new_speed, pwm_motion=False):
        # Sets the speed in degrees per second
        if pwm_motion:
            if self.pwm == None:
                self.pwm = machine.PWM(self.s)
        else:
            if self.pwm != None:
                self.pwm.deinit()
            self.pwm = None
        if new_speed == 0:
            if self.pwm:
                self.pwm.duty(0)
            self.stepping = False
        else:
            if new_speed < 0:
                self.set_dir(1)
            else:
                self.set_dir(0)
            self.stepping = True
            # Int for speed of calculation inside the tight loop fite me.
            self.step_interval = int(1e6*(1/(abs(new_speed)*REAL_STEPS_PER_DEGREE))/2)
            self.move_start_ticks_us = ticks_us()
            self.move_start_index = self.index
            if self.pwm != None:
                self.freq = int(abs(new_speed)*REAL_STEPS_PER_DEGREE)
                self.pwm.freq(self.freq)
                self.pwm.duty(int(self.freq/2))

        if self.debug: print("New speed: {}".format(new_speed))
        self.debug_blast()

    def set_dir(self, new_dir):
        self.dir = new_dir
        self.d.value(1-self.dir)

    def debug_blast(self):
        if not self.debug:
            return
        if self.name: print("Name: {}".format(self.name))
        print("step_interval: {}".format(self.step_interval))
        print("Stepping: {}".format(self.stepping))
        print("homing: {}".format(self.homing))
        print("indexed: {}".format(self.indexed))
        print("Index: {}".format(self.index))
        print("target index: {}".format(self.target_index))
        if self.pwm != None:
            print("Freq: {}".format(self.freq))
        if self.hall_effect:
            print("Hall effect: {}".format(self.o.read()))
        print("--------------------")

    def set_angle(self, angle, speed=DEFAULT_MOVE_SPEED, pwm_motion=False):
        if not self.indexed:
            print("Cannot set angle. Not indexed.")
            self.debug_blast()
            return
        angle %= 360
        self.target_index = int(angle*REAL_STEPS_PER_DEGREE)
        diff = self.target_index - self.index
        if self.debug:
            print("Set angle: {}".format(angle))
            print("Index diff: {}".format(diff))
        if abs(diff) < INDEX_CLOSE_ENOUGH:
            self.set_speed(0)
            return
        # If you can think of a cleaner, more readable version of this please let me know.
        if abs(diff) < REAL_STEPS_PER_REV/2:
            # Going straight there is faster.
            if diff < 0:
                self.set_speed(-speed, pwm_motion=pwm_motion)
            else:
                self.set_speed(speed, pwm_motion=pwm_motion)
        else:
            # Cross zero to get there
            if diff > 0:
                self.set_speed(-speed, pwm_motion=pwm_motion)
            else:
                self.set_speed(speed, pwm_motion=pwm_motion)

    def set_enabled(self, enabled):
        # The stepper is enabled on logical 0.
        enabled = 1 - enabled
        self.enabled.value(enabled)

    def home(self):
        self.indexed = False
        self.index = -1
        self.target_index = -1
        self.homing = True
        self.set_speed(HOME_SPEED)

    def opto_rise(self):
        # Returns true if the optoswitch went high since the last check
        returnVal = False
        if self.last_o == 0 and self.o.value() == 1:
            returnVal = True
        self.last_o = self.o.value()
        return returnVal
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

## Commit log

2020-04-12 More working.
    [Pulley_T-MXL-XL-HTD-GT2_N-tooth.scad, holders.scad]
2020-04-12 Add readme, and something else I don't remember.
    [holders.scad]
2020-04-13 Add arm1
    [holders.scad]
2020-04-13 Add a link to the belt length calculator.
    [holders.scad]
2020-04-13 Fix whitespace
    [holders.scad]
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2020-04-13 Add a guide to the other side shaft 1 drive gear.
    [holders.scad]
2020-04-13 Fix the split on arm1
    Add shaft 2 driven pulley
    [holders.scad]
2020-04-13 Add bottom bearing mount stuff.
    [holders.scad]
2020-04-14 Make arm slots work better.
    [holders.scad]
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2020-04-15 Beef up lip on shaft 2 driven pulley.
    Add arm2
    [holders.scad]
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2020-04-15 Add an assembled view.
    Add optoflags and an optoswitch holder.
    [holders.scad]
2020-04-16 Tweak for printing.
    [holders.scad]
2020-04-16 Add PCB design. Not routed yet.
    [sand_drawing.kicad_pcb, sand_drawing.sch]
2020-04-17 Add jumpers for microstepping.
    [sand_drawing.sch]
2020-04-17 Rearrange stuff, start routing.
    [sand_drawing.sch]
2020-04-18 More traces
    [sand_drawing.kicad_pcb]
2020-04-18 Add flood fills.
    Add silkscreen text for spare pins.
    [sand_drawing.kicad_pcb, sand_drawing.sch]
2020-04-18 Tidy up schematic.
    [sand_drawing.kicad_pcb, sand_drawing.sch]
2020-04-18 Add the basics of some stepper control. Still not working perfectly.
    [sand_drawing.py]
2020-04-19 Add debug
    Fix multi-axis movement
    Add easy toggle for wild mode.
    [sand_drawing.py]
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2020-04-19 Rotate pin holding arm1 to shaft1 to allow it to be tapped through.
    [holders.scad]
2020-04-19 Fix GH issue #2 by splitting arm1 horizontally not vertically.
    [holders.scad]
2020-04-19 Use the split version of arm1 in the assembled module.
    [holders.scad]
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2020-04-23 Add a flag to disable MQTT checking, and check for new patterns on a timer.
2020-04-23 Break the PWM stepping out to a setting separate to the microcontroller. This code gets 3.7s revolutions on an ep32.
2020-04-25 Removed the program-wide PWM stepping setting in favour of G0 - Fast move gcode.
    Not fully implemented yet.
2020-04-25 Some refactoring, spam prevention, etc.
    [sand_drawing.py]
2020-04-25 Track index on G0 moves. First test showed this doesn't work quite right.
    [sand_drawing.py]
2020-04-25 Working on handling fast movements overshooting their target by good margins.
    [sand_drawing.py]
2020-04-25 Shockingly broken in most ways.
    [sand_drawing.py]
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2020-05-10 Added arm2optoarm for homing Y axis.
    [holders.scad]
2020-05-11 Made arm2 a bit thinner to give more clearance for the arm2 opto.
    [holders.scad]
2020-05-12 Beginning to work on the bounds-limiting code to stop the arm hitting the sides of the enclosure.
    This doesn't work yet. I've added test_coordinate_bounds.py to check things out off-board.
    [cnc.py, constants.py, test_coordinate_bounds.py]
2020-05-12 Handle import failure better when running off-target.
    Fix demo case.
    [cnc.py, test_coordinate_bounds.py]
2020-05-12 Fix closest two points calculation.
    [cnc.py]
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2020-05-12 Fix arm length, fine-tune homing index zero points.
    [cnc.py, constants.py, test_coordinate_bounds.py]
2020-05-13 Remove commented-out path speed compensation. Probably won't need it.
    [cnc.py]
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2020-05-15 Setting up pattern generator support woo.
    [holders.scad]
2020-05-15 Generators now working!
    Added a note about the generator try/catch bug. Need to document the generator spec now.
    [cnc.py, pub_gen.py]
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2020-05-16 A fairly substantial rework of homing logic. Should work better now.
    [cnc.py, stepper.py]
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2020-05-19 Start the work involved in transitioning to the ESP-WROOM-32D and TMC2100.
    [sand_drawing.kicad_pcb]
2020-05-22 More work on adding the esp32 .
    [sand_drawing.sch]
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2020-05-25 Avoid starting drawing a circle near the centre.
    [pub_gen.py]
2020-05-26 Redesigned for ESP32 and TMC2100s. Lots more work to go.
    [sand_drawing.kicad_pcb]
2020-05-28 Assigning JLCPCB parts store codes to stuff.
    [BOM.csv, sand_drawing.kicad_pcb, sand_drawing.sch]
2020-05-28 Finished hooking up the EN and IO0 buttons.
    [sand_drawing.kicad_pcb, sand_drawing.sch]
2020-05-28 Fix weird link count issue on my desktop...
    [sand_drawing.sch]
2020-05-28 Update BOM and beginning to lay out the new PCB.
    [sand_drawing.csv, sand_drawing.kicad_pcb]
2020-05-28 Protection diodes placed.
    [sand_drawing.kicad_pcb]
2020-05-29 Nearly finished PCB layout.
    [sand_drawing.kicad_pcb, sand_drawing.sch]
2020-05-29 More or less done. It needs to be a bit narrower, so I'm going to rejig the mounting holes.
    [sand_drawing.kicad_pcb, sand_drawing.sch]
2020-05-30 Final tweaks. v1.0 PCB done!
    [BOM.csv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]
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2023-10-04 PCB updates, stepper control changes.
    [sand_drawing.kicad_pcb]
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2023-10-08 Lasercut version
    [holders.scad]
2023-10-10 Lasercut stuff work.
    [holders.scad]
2023-10-10 add todo
    [holders.scad]
2023-10-10 Add kerf to top holder
    [holders.scad]
2023-10-11 Automate dxf export
    [holders.scad]
2023-10-15 Add belt splitter
    [holders.scad]
2023-10-15 Getting there
    [holders.scad]
2023-10-15 Adjustable lasercut arm1
    [holders.scad]
2023-10-18 Minor pin changes
    [holders.scad]
2023-10-18 Enclosure work.
    [holders.scad]
2023-10-18 Use 12 pins for outer ring.
    [holders.scad]
2023-10-18 More enclosure work.
    [holders.scad]
2023-10-18 Add a reasonably silly flexure idea on arm1
    [holders.scad]
2023-10-18 A somewhat more promsing flexure design.
    [holders.scad]
2023-10-18 Flexure tweaks
    [holders.scad]
2023-10-21 Add bed and stuff.
    [holders.scad]
2023-10-22 Fix bed and felt exports
    [holders.scad]
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2023-10-22 Update PCB and schematic to map all stepper control pins to GPIO.
    [sand_drawing.kicad_pcb, sand_drawing.kicad_sch]
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2023-10-25 Working on new vreg
    [sand_drawing.kicad_sch]
2023-10-29 v1.1 of the PCB nearly done.
    [sand_drawing.kicad_pcb, sand_drawing.kicad_sch]
2023-10-30 Updated to kicad v7.0.8.
    [sand_drawing.kicad_pcb, sand_drawing.kicad_sch]
2023-10-30 Update footprints.
    [sand_drawing.kicad_pcb, sand_drawing.kicad_sch]
2023-12-11 Add DXFs for lasercut design.
    [arm_1_lasercut_adjustable_x4.dxf, arm_1_pulley_lasercut_x2.dxf, arm_2_lasercut_x1.dxf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]
2024-10-05 Minor tweaks to PCB. Thicker 12v rail, rearranged 3.3v connection to drivers, thicker connection between PSU and inductor.
    [sand_drawing.kicad_pcb]
2024-10-06 PCB v1.1
    [sand_drawing.kicad_pcb, sand_drawing.kicad_sch]
2024-10-06 Tweaks to PCB. Finding parts.
    [sand_drawing.kicad_pcb, sand_drawing.kicad_sch]
2024-10-06 Updated part numbers and footprints.
    [sand_drawing.kicad_pcb, sand_drawing.kicad_sch]
2024-10-31 Updated DXFs
    [arm_1_lasercut_adjustable.dxf, base_guide_lasercut_x4.dxf, base_lasercut_x2.dxf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]
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2024-10-31 PCB DRC and label fixes.
    [sand_drawing.kicad_sch]
2024-11-01 Add notes to readme, bump version number in schematic drawing, add PCB changelog.
    [sand_drawing.kicad_sch]
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2024-11-01 Remove old BoM, add note to readme.
    [BOM.csv]
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
